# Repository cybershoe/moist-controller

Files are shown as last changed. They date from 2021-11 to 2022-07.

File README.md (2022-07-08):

# moist-controller
[][cc-by-sa]

## Overview

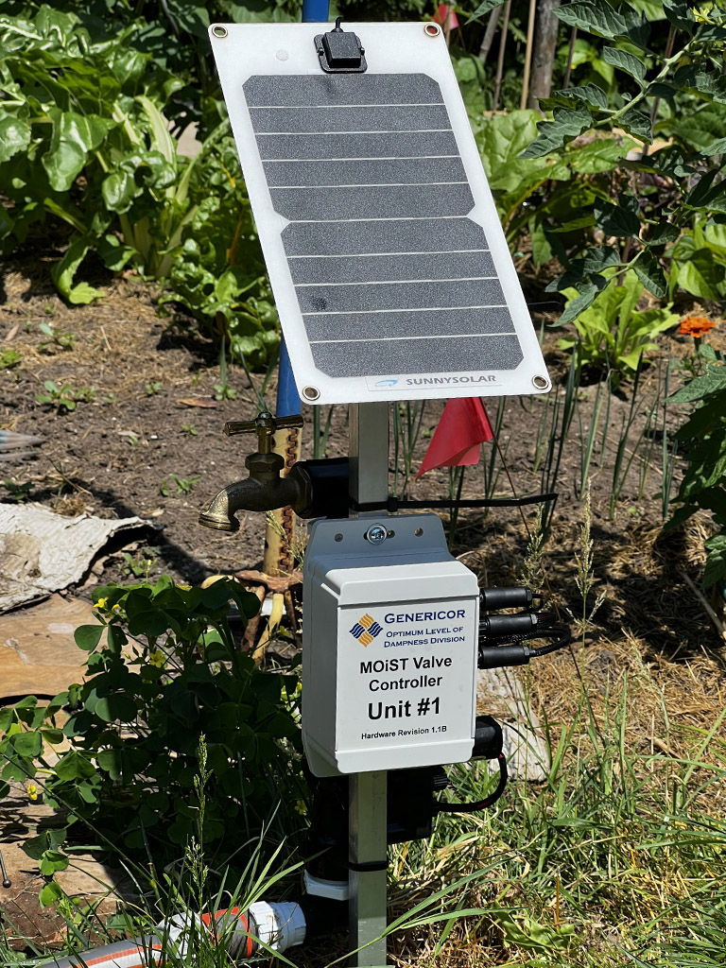
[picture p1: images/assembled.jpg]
Assembled Valve


The Moisture-Optimization through Solar Technology (MOiST) Controller is a distributed, solar-powered, ESP8266-based
controller that exposes standard irrigation valves into [Home Assistant](https://www.home-assistant.io/) through
the [ESPHome](https://esphome.io/) component.

The MOiST valve is designed to be:

### Simple

The controller does one thing: control a valve. Once added into Home Assistant, the controller exposeses a switch that
opens or closes the valve, sensors for water flow rate and total water consumption, and battery power monitoring. That's
it. You are free to use whatever mechanism you want to manage the valves, including HA automations, Node-RED flows, or
any other platform that integratges with Home Assistant.

### Flexible

This project started because we change up our gardens frequently, and we couldn't predict in advance where we would want
automatic irrigation, or how the yard would be zoned. The idea behind the controller is that you can mount your valve, 
controller, and solar panel on a stake, stick it in the ground where you need it, point it South (or North if you're in
the Southern Hemisphere), hook it up to a hose and be up and running quickly. Buried valves with hardwired power look
nicer, and would be more appropriate for a lawn, but for a food garden, this design provides more flexibility. The
controller should be able to drive any standard irrigation valve that uses a 9V DC latching solenoid.

### Self-contained

Running hoses is one thing, running power is another. The controller was designed to minimize power consumption to a
point where it can run off of a 5-Watt, 6-Volt solar panel and a 18650 battery with the amount of sun available during
growing season. Components were selected for low quiescent power, and the most inefficient parts of the controller are
powered off unless actively being used. On a quiet WiFi network, power consumption averages around 30mA

## Usage

- Install a charged 18650 battery and press the "START" button to enable the battery protection circuit
- Connect a 3.3v USB to TTL adapter to the UART pin header JP1
- Install the ESPHome firmware with [this configuration](/moist-valve.yaml)
- Connect a 6V 1W solar panel to PV IN
- Connect your 9V latching irrigation valve solenoid to SOL
- Connect your water flow meter to METER
- Place the valve where the solar panel will receive full sun, connect your hoses, and begin MOiSTening your plants!

## Theory of Operation
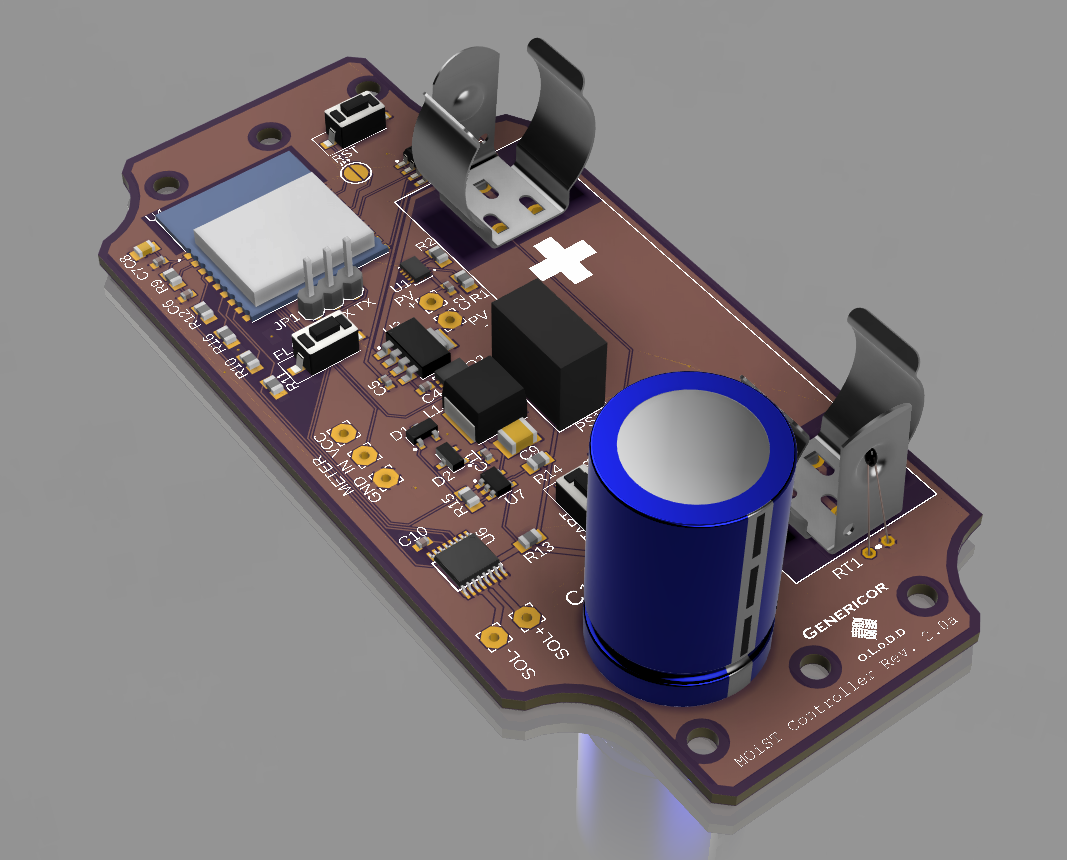
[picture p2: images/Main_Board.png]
Board Render

Schematic

The controller has 3 main functional areas: battery and power management, the solenoid driver, and the MCU.

### MCU (ESP8266)

The ESP8266 U5 is the heart of the system. It is running the ESPHome firmware, which handles the various outputs and sensors.
A bare ESP-WROOM-02D module was used rather than something like a D1 Mini, in order to remove unnecessary components and
minimize power requirements (USB-UART, LEDs, 5v regulator, etc.)

### Battery and Power Management

The system uses a standard 18560-style, unprotected Li-ion battery. Over-charge, over-discharge, over-current, and short
protection are provided by a BQ29733 protection IC U2, and solar charging is handled by a BQ24210 solar charger U1 in battery
tracking mode, to maximize charging ability with low solar panel outputs. The charger can take any 6-volt solar panel, and
will charge at up to 800 mA. An LP3693MPX LDO regulator U3 provides 3.3V to the the rest of the components. An INA219 I2C
wattmeter U5 monnitors the battery voltage and current flowing in/out of the battery.

### Solenoid Driver

The solenoid driver consists of an unregulated boost converter PS1 that raises the 3V3 rail up to ~9V, a capacitor C1 to store
enough energy to drive the solenoid, an H-bridge driver U6 to drive the solenoid in the appropriate direction, and a comparator 
U7 with an 8.2V reference D2 to indicate when the capacitor is sufficiently charged. To open or close the solenoid, the MCU first
sets the DRV_EN pin HIGH, which powers up the boost converter and enables the H-Bridge. After a short delay for the comparator
to stabilize, the MCU waits for the capacitor voltage to exceed the 8.2v reference, causing the comparator to bring the
!CHGD line LOW. Once the capacitor is charged, the MCU pulses the DRV_1 or DRV_2 pin HIGH for the appropriate duration to open or
close the valve, respectively, and then brings DRV_EN low to power off the driver circuitry and preserve energy.

## A Note about WiFi:

ESP power consumption is significantly affected (sometimes by a factor of 2 or more) by how long the modem can stay in sleep mode.
To minimize power consumption, consider the following:

- Increase your DTIM beacon interval. This increases how long the ESP can stay asleep before waking up to check for data.
- Broadcast traffic causes the modem to wake up, including mDNS. Consider creating a separate WLAN and subnet for your low-power ESP devices, and use static IPs in ESPHome to minimize the amount of broadcast traffic reaching the ESPs.

## Current status and next steps

### 2022-07-04
- Added solder jumper between GPIO16 and RST to allow deep sleep
- Redesigned board to fit Hammond 1555FF43GY enclosure
- Ordered redesigned boards (Rev 2.0A)

### 2022-07-04
- Working first revision hardware completed: [Video](https://youtu.be/AA5Or_j-FIE)
- Abandoned 3D printed custom enclosure, used off-the-shelf Hammond enclosure and a mounting plate for the Rev. 1.1B boards
- 3D printed a bracket to mount the solar panel at a 45° angle on a 3/4" square aluminium post

### 2021-11-18
- Fixed incorrect boot mode pull-up/down resistors
- Added reset button
- Renamed BOOT button to FLASH
- Added mounting hole instead of using 3d printed cantilever clips
- Ordered Rev 1.1B boards

### 2021-11-06:
The breadboard prototype is functionally complete, and an order has been placed with OSHPark for a batch of boards for a
final prototype. 

### TODO:
- NodeRED flows for irrigation timing
- Optimize board for smaller enclosure

This work is licensed under a
[Creative Commons Attribution-ShareAlike 4.0 International License][cc-by-sa].

[][cc-by-sa]

[cc-by-sa]: http://creativecommons.org/licenses/by-sa/4.0/
[cc-by-sa-image]: https://licensebuttons.net/l/by-sa/4.0/88x31.png
[cc-by-sa-shield]: https://img.shields.io/badge/License-CC%20BY--SA%204.0-lightgrey.svg

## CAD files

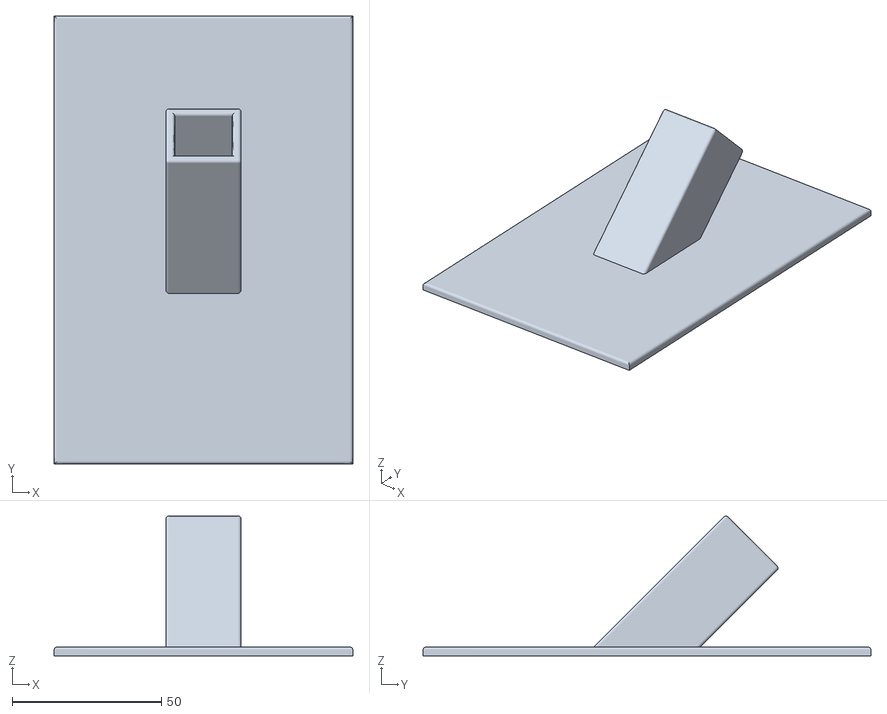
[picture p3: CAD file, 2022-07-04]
hardware/Solar Panel Mount.stl
100.0 x 150.0 x 46.9

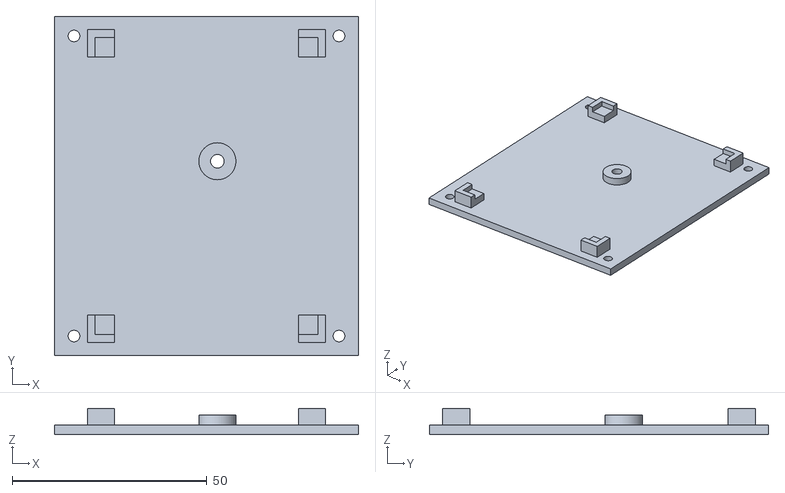
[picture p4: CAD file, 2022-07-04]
hardware/MOIST prototype bracket.stl
78.0 x 87.0 x 6.75

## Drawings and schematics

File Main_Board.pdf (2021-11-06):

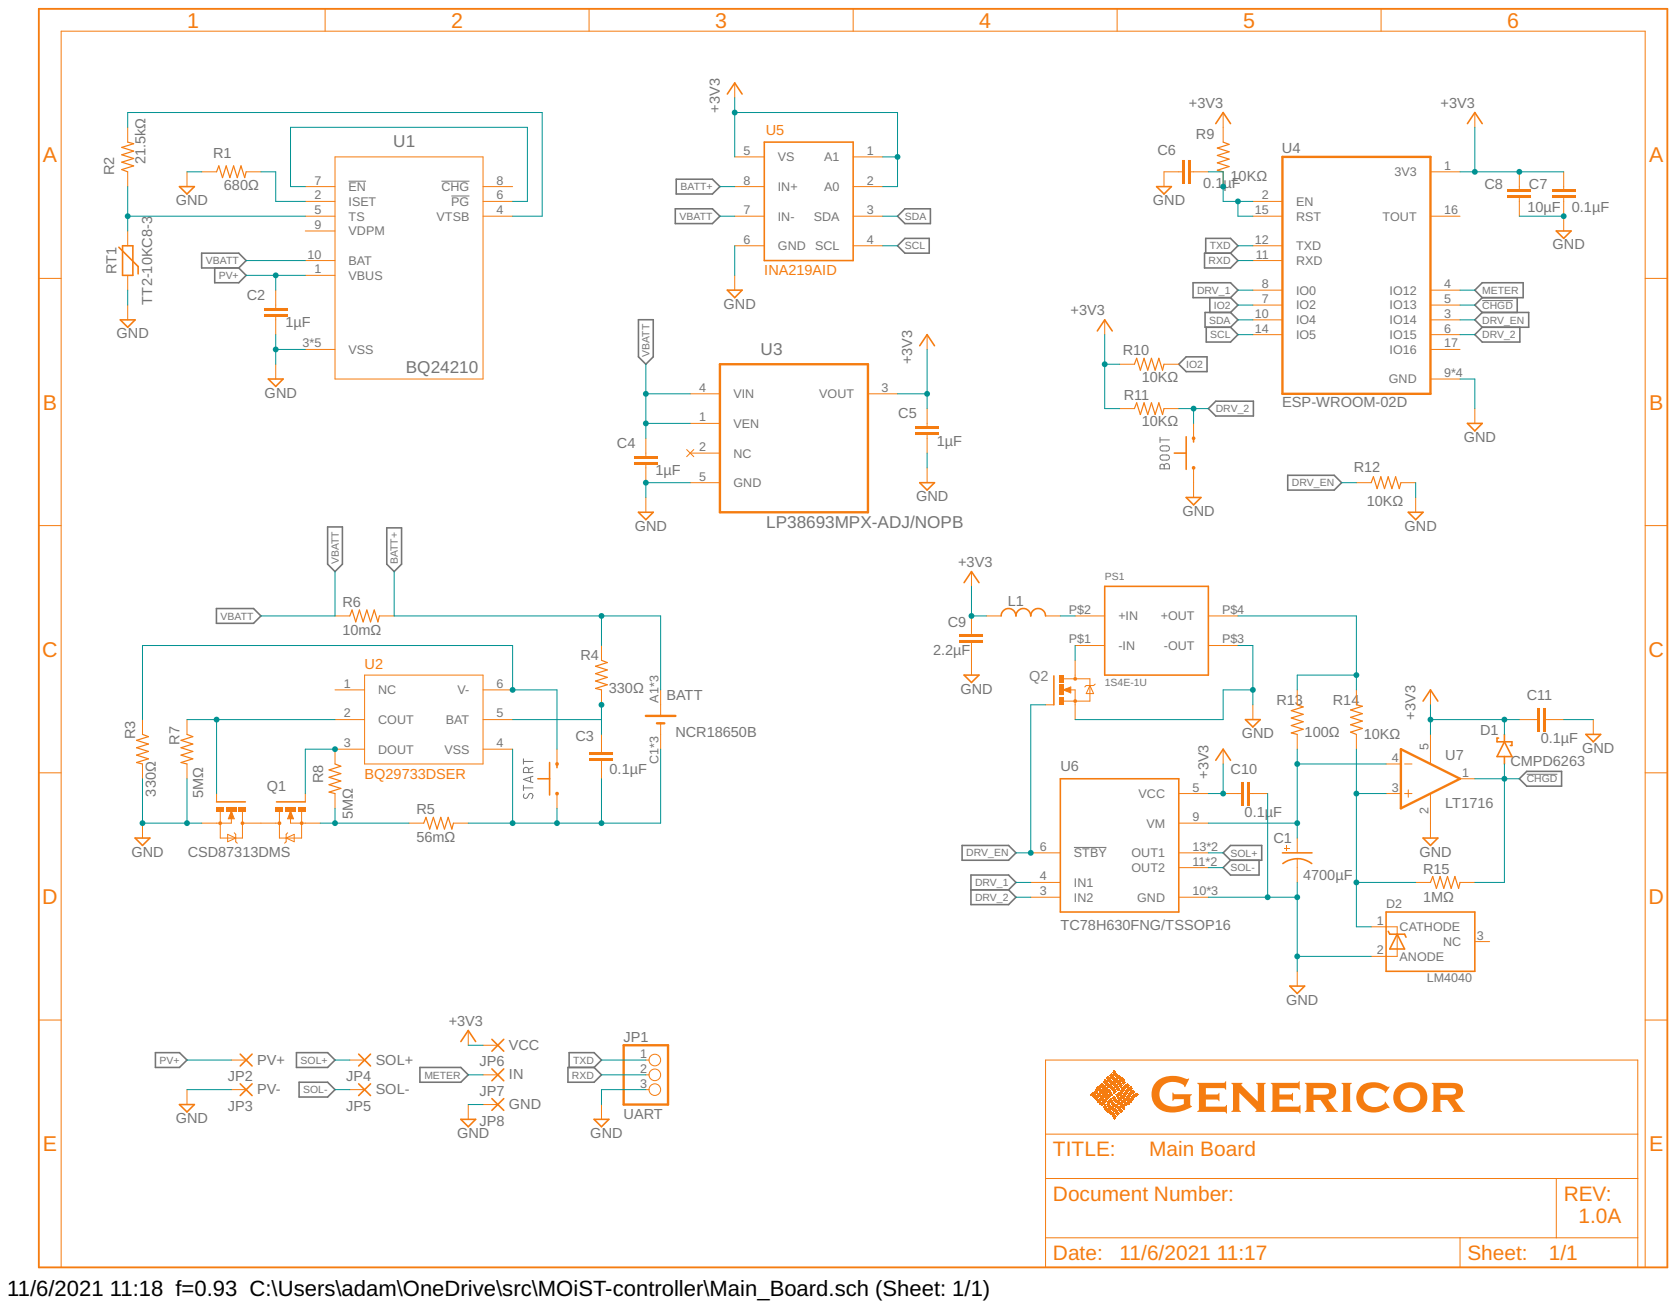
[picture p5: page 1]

Document Number: | REV: 1.0A

Date: 11/6/2021 11:17 | Sheet: 1/1

11/6/2021 11:18 f=0.93 C:\Users\adam\OneDrive\src\MOiST-controller\Main_Board.sch (Sheet: 1/1)

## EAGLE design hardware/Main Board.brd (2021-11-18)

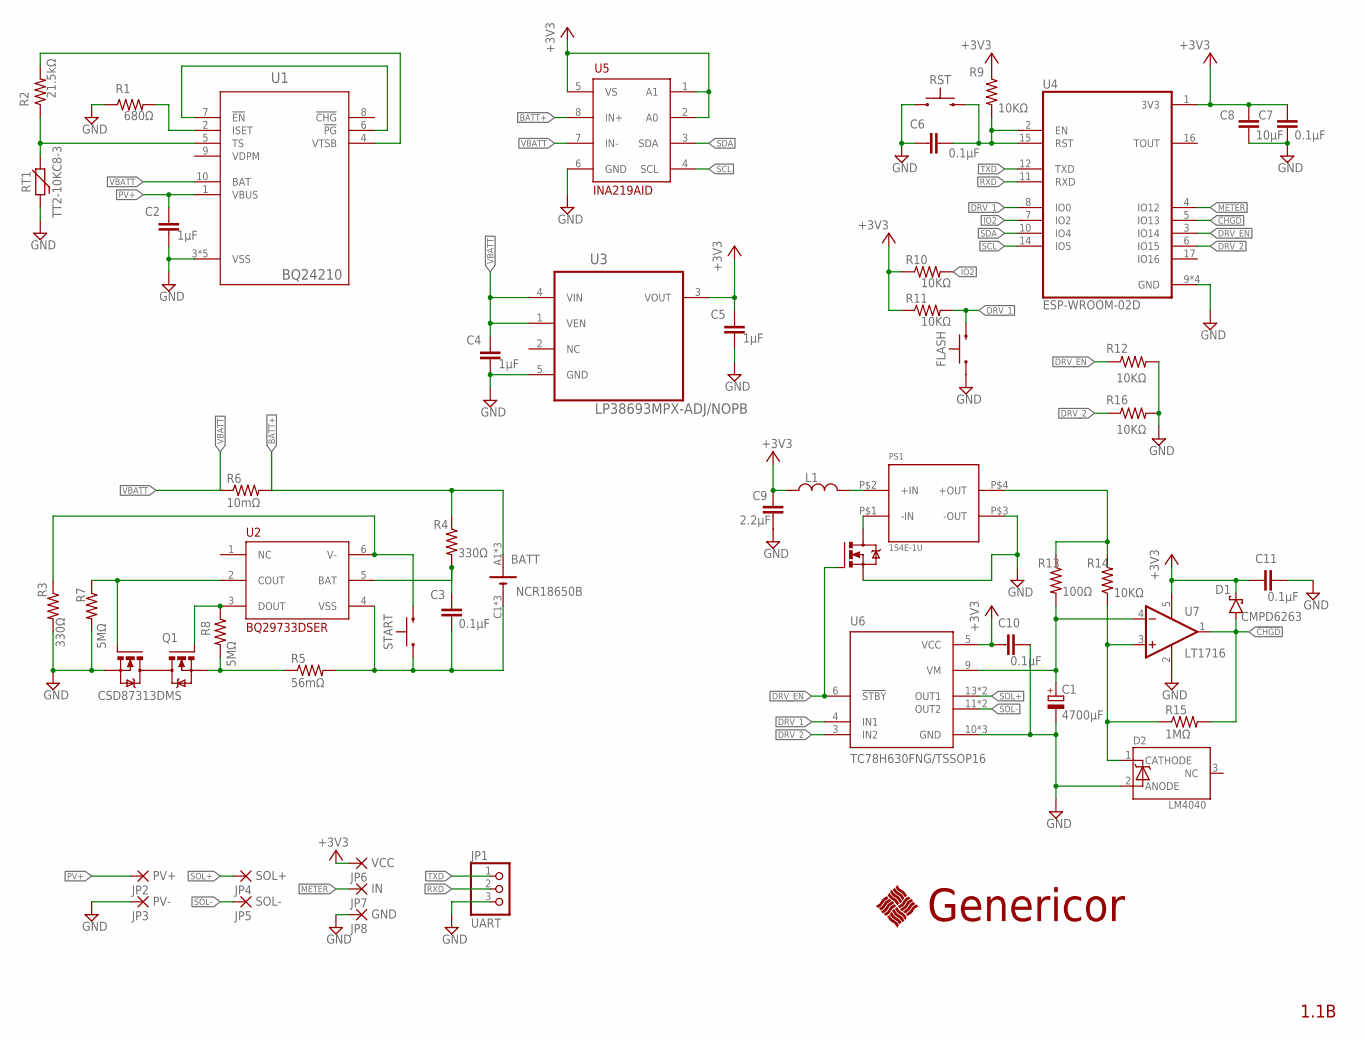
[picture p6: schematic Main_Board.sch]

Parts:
BATT: NCR18650B; 18650-65MM-54-PTH
C1: 4700µF; E7,5-18
C2, C4, C5: 1µF; C0402
C3, C6, C7, C10, C11: 0.1µF; C0402
C8: 10µF; C0805
C9: 2.2µF; C1210
D1: CMPD6263; SOT95P227X109-3N
D2: LM4040LM4040CIM3-8.2; SOT95P240X110-3N
FLASH: PTS636_SL43_SMTR_LFS; S_43
JP1: UART; 1X03
JP2: PV+; 2,54/1,1
JP3: PV-; 2,54/1,1
JP4: SOL+; 2,54/1,1
JP5: SOL-; 2,54/1,1
JP6: VCC; 2,54/1,1
JP7: IN; 2,54/1,1
JP8: GND; 2,54/1,1
L1: ASPI-6045S-180M-T; INDM6060X450N
PS1: 1S4E-1U; 1S4E_S1U-DIP4
Q1: CSD87313DMS; DMS0008A
Q2: CSD16406Q3; DQG0008A
R1: 680Ω; R0805
R2: 21.5kΩ; R0805
R3, R4: 330Ω; R0805
R5: 56mΩ; R0805
R6: 10mΩ; R1206
R7, R8: 5MΩ; R0805
R9, R10, R11, R12, R14, R16: 10KΩ; R0805
R13: 100Ω; R0805
R15: 1MΩ; R0805
RST: PTS636_SL43_SMTR_LFS; S_43
RT1: TT2-10KC8-3; THERMISTOR
START: PTS636_SL43_SMTR_LFS; S_43
U1: BQ24210; DQC10_P84X2P4
U2: BQ29733DSER; SON50P150X150X80-6N
U3: LP38693MPX-ADJ/NOPB; SOT150P700X180-5N
U4: ESP-WROOM-02D; MODULE_ESP-WROOM-02D
U5: INA219AID; SOIC127P599X175-8N
U6: TC78H630FNG/TSSOP16; TSSOP16
U7: LT1716; SOT95P280X100-5N
U$2: GENERICORLOGO

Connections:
8.2VREF: D2.1 (CATHODE), R14.1, R15.1, U7.3 (IN+)
9V+: PS1.P$4 (+OUT), R13.1, R14.2
!CHGD: D1.1 (A), R15.2, U4.5 (IO13), U7.1 (OUT)
+3V3: C5.1, C7.1, C8.1, C9.1, C10.1, C11.1, D1.3 (C), JP6.1, L1.1, R9.1, R10.1, R11.1, U3.3 (VOUT), U4.1 (3V3), U5.1 (A1), U5.2 (A0), U5.5 (VS), U6.5 (VCC), U7.5 (V+)
BAT: C3.1, R4.2, U2.5 (BAT)
BATT+: BATT.A1 (+), BATT.A2 (+), BATT.A3 (+), R4.1, R6.2, U5.8 (IN+)
BATT-: BATT.C1 (-), BATT.C2 (-), BATT.C3 (-), C3.2, R5.2, START.A (1), U2.4 (VSS)
COUT: Q1.4 (G2), R7.1, U2.2 (COUT)
DOUT: Q1.1 (G1), R8.1, U2.3 (DOUT)
DRV_1: FLASH.C (2), R11.2, U4.8 (IO0), U6.4 (IN1)
DRV_2: R16.1, U4.6 (IO15), U6.3 (IN2)
DRV_EN: Q2.4 (G), R12.1, U4.3 (IO14), U6.6 (!STBY)
EN-RST: C6.1, R9.2, RST.C (2), U4.2 (EN), U4.15 (RST)
GND: C1.-, C2.2, C4.2, C5.2, C6.2, C7.2, C8.2, C9.2, C10.2, C11.2, D2.2 (ANODE), FLASH.A (1), JP1.3, JP3.1, JP8.1, PS1.P$3 (-OUT), Q1.5 (S2), Q1.6 (S2), Q1.10 (S2), Q2.1 (S), Q2.2 (S), Q2.3 (S), R1.1, R3.2, R7.2, R12.2, R16.2, RST.A (1), RT1.1, U1.3 (VSS), U1.11 (VSS), U1.V (VSS), U1.V_1 (VSS), U1.V_2 (VSS), U3.5 (GND), U4.9 (GND), U4.13 (GND), U4.18 (GND), U4.19 (GND), U5.6 (GND), U6.10 (GND), U6.15 (GND), U6.16 (GND), U7.2 (V-)
IO2: R10.2, U4.7 (IO2)
ISET: R1.2, U1.2 (ISET)
METER: JP7.1, U4.4 (IO12)
PG-EN: U1.6 (!PG), U1.7 (!EN)
PS1+IN: L1.2, PS1.P$2 (+IN)
PS1-IN: PS1.P$1 (-IN), Q2.5 (D), Q2.6 (D), Q2.7 (D), Q2.8 (D), Q2.9 (D)
PV+: C2.1, JP2.1, U1.1 (VBUS)
Q1S1: Q1.7 (S1), Q1.8 (S1), Q1.9 (S1), R5.1, R8.2
RXD: JP1.2, U4.11 (RXD)
SCL: U4.14 (IO5), U5.4 (SCL)
SDA: U4.10 (IO4), U5.3 (SDA)
SOL+: JP4.1, U6.13 (OUT1), U6.14 (OUT1)
SOL-: JP5.1, U6.11 (OUT2), U6.12 (OUT2)
TS: R2.1, RT1.2, U1.5 (TS)
TXD: JP1.1, U4.12 (TXD)
V-: R3.1, START.C (2), U2.6 (V-)
VBATT: C4.1, R6.1, U1.10 (BAT), U3.1 (VEN), U3.4 (VIN), U5.7 (IN-)
VM: C1.+, R13.2, U6.9 (VM), U7.4 (IN-)
VTSB: R2.2, U1.4 (VTSB)

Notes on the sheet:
Genericor
1.1B

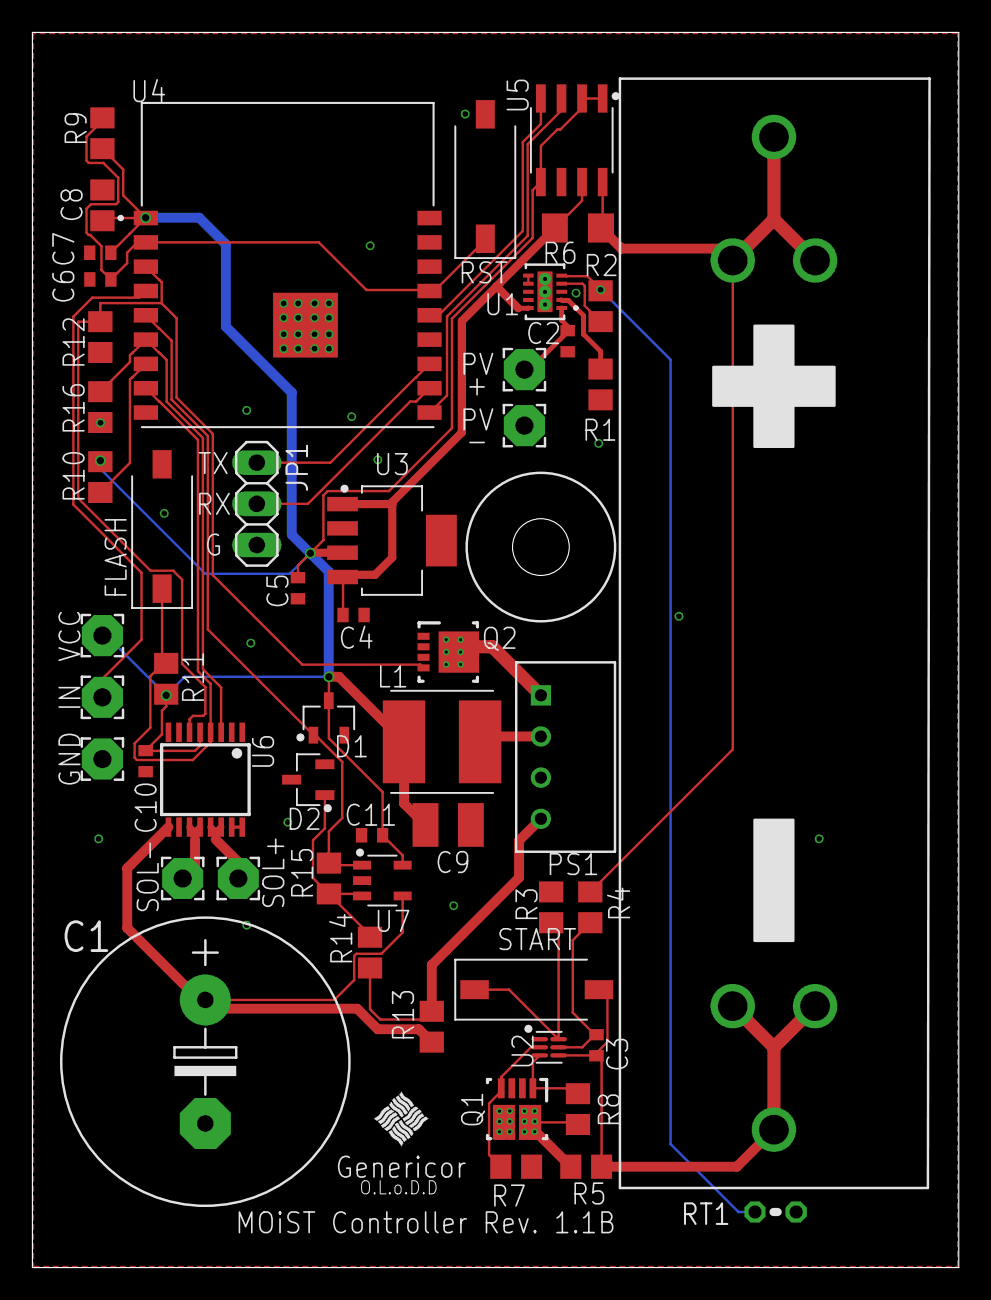
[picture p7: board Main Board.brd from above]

Board: 2 copper layers, 57.1 x 76.2 mm, 54 parts (0 on the bottom side), 33 nets.

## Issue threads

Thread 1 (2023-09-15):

How to open brd file?

n8henrie, 2023-09-15:
This seems like a really cool project, thanks for sharing!

I've been hoping to make a similar project for years -- have the ESPs, the 18650s, the 6v solar panels, but never made much progress beyond that. Was really excited to find this!

Unfortunately I'm not able to open the brd files in Kicad -- it seems to have an option to import Eagle files (I assume you used Eagle to create these?) but then fails apparently due to an unrecognized character in the BRD file.

Can you provide any more details on how to created the schematics, and what other users can use to create the circuitboard?

cybershoe, 2023-09-15:
I use Fusion360 for my workflow (the free-for-personal-use version). If you just want to get boards made, you can submit the .zip in the hardware directory to your fab (I use OSH Park, but there aren't any crazy tolerances on the board, so I'd imagine most fabs should be able to take the files as they are).

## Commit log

2021-11-06 Create Main_Board.svg
    Add SVG of Schematic
2021-11-06 Add WiFi power note
2021-11-08 Move hardware, add example config
    [Main Board.brd, Main_Board.sch]
2021-11-08 Add UART pinout
2021-11-08 Pin swap in docs
2021-11-18 Update docs for Rev 1.1B changes
    [Main Board.brd, Main_Board.sch]
2022-07-04 1st fully-functional valve
    [MOIST prototype bracket.stl, Solar Panel Mount.stl]

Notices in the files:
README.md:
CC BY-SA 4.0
